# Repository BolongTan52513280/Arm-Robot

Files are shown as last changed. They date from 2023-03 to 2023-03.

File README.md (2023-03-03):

# Arm-Robot
A robot arm is developed. The robot arm consists of a base, two arms, two motors, two 
worm gears, two face-mount crossed-Roller bearings, two sensors, one pcb board and one 
Arduino board. 
此机械手臂机器人可抓取任何 15Kg 以下的物体并转移到指定地点。工作空间直径 1.4m, 稳定时间 1.3s, 超调为 5%，稳态误差 2.5%。
可用于物品运输，组件组装。我负责利用 Solidworks 设计机器人机械设计，并使用 Matlab 和 Simulink 设计控制系统，也负责机器人的测试，调试工作。

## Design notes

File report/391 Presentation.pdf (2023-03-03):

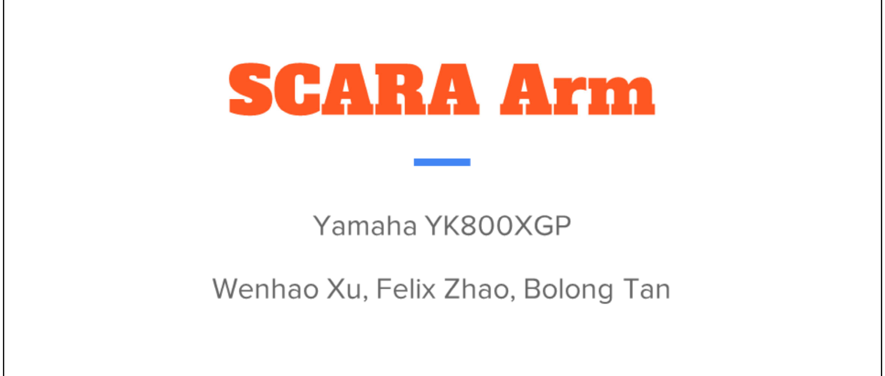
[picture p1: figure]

This slide deck will be for our final presentation for ELEC391 SCARA ARM. For team Yamaha YK800XGP.

For team organization, we split the work equally, Wenhao took care of the software section
Felix took care of the hardware section
And Bolong took care of the system section.
We also collaborate and help each other on their parts whenever possible.

For Electrical systems ECG, we need to design a circuit that will be able to support our motor selected.
We need to have a consistent nominal voltage and current that can satisfy our motors rated voltages.
We also need to not draw more current than we want from the wall plug to trigger the normally present wall plug fuses.
Our motor control board need to have a high switching frequency to reduce general component sizes and reduce our PCB size to be able to fit into our design’s base cavity. Lastly, of course we need basic circuit protection like overcurrent protections, voltage/current isolation, voltage/current surge protections and overheat protections.

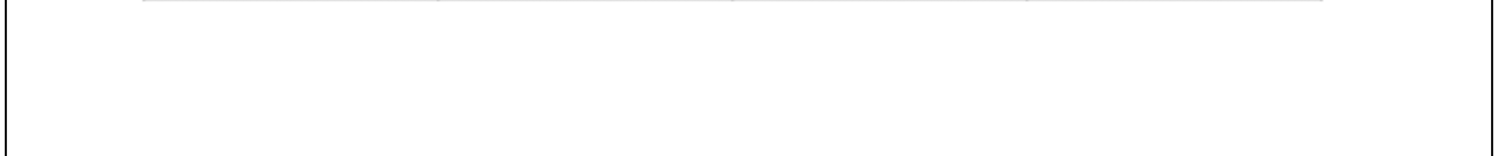
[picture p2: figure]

This is our mechanical system RCG.
The work space diameter we want to achieve is 1.2m and the height is 550mm.
One of our robot arm is 350mm and the other one is 250mm in length.
The full length of our robot arm is 600mm. The work space diameter is 2*600mm= 1.2m. The robot arm can reach any points within the work space.
For the payload, our goal is 15kg.
In our simulink and simulationx model,we used the 15kg load to simulate the whole model.
Even though the inertia due to the robot arm and 15Kg is pretty large.
Our design have successfully meet all these requirements.

This is our control system RCG. First we want an accurate arm, so we want to minimize steady state error and overshoot. We also want a fast arm, so we want to have good settle time and rise time.

As you can see this is our explode animation with the extra feature.

Our design consists of one base, three robot arms, three motors, three worm gears etc.

Two robot arms can move in the horizontal plane. Both arms can rotate 360 degree.

Our robot arm can also move in Z direction.

We used one extra motor and one extra worm gear.
1. Motor rotate shaft which is connected to worm gear (gear ratio is 30)
1. Worm gear is connected to the lead screw through the shaft
1. Worm gear and leads screws rotates at the same speed
1. A hex nut which connected to a rod is used
1. Hex nut cannot rotate because it is surrounded by a shell
1. Lead screw forces the hex nut to move up or down

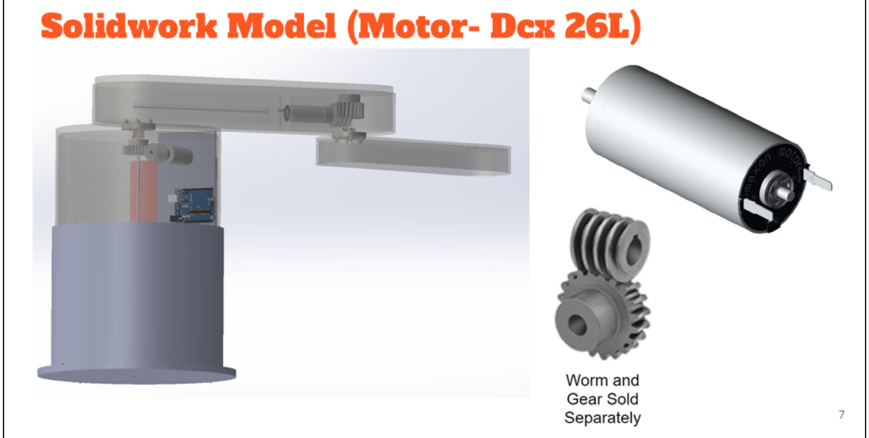
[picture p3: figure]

This is the solid work model we use without extra features whose arm can only move in horizontal plane.

Two robot arms can move in the horizontal plane. Both arms can rotate 360 degree.

The design consists of one base,two robot arms and two motors, two worm gears and etc.

The motor we chose is Dcx-26L.The reason we chose this motor is that:

1. Our robots arm length is 600mm which is quite long
1. We also want to pick a 15kg object

According to the calculation the torque we need is around 50Nm. The Dcx-26L motor is fits our requirement best.

Gear ratio of two worm gears we used are 20 and 30.

The advantage of worm gear is that:

1. Cheaper
1. Do not require too much space ( can be easily put into robot arm)

Two face-mount crossed-Roller bearing are used to make sure both robot arms can rotate freely in horizontal plane.

One face-Mount crossed-Roller bearing is used to connect base to arm.

The other one is used to connect two arms together.

For one of face-mount crossed-Roller bearing:

The inner part of face-mount crossed-Roller bearing is connected to the base using screws and nuts.

The inner part is fixed with respect to base.

The outer part of face-mount crossed-Roller bearing is connected to the robot arm using screws and nuts. It rotates at the same speed with arm.

For the other face-mount crossed-Roller bearing:

The inner part of face-mount crossed-Roller bearing is connected to the upper arm using screws and nuts.

The inner part is fixed with respect to upper arm..

The outer part of face-mount crossed-Roller bearing is connected to the lower robot arm using screws and nuts. It rotates at the same speed with lower arm.

For our power supply board design, with the previously mentioned RCG in mind, we developed out board to have:

- 5V, 12V and 24V output support for all the external ICs we need. (Arduino, Motor, Sensor)
- 40A maximum current supplied to the motor output.
- Stable voltage output under high current applications. (24±0.3V under 25A, 24±1V under 40A)
- Safety fuses in case of current surges for each output and transformers to prevent meltdowns.
- LED indicators and test points for easy debugging.
- Different thickness traces for high/low current areas, mounting holes for installation of the board, and a slot for arduino board.

The resulted board is able to support 2 26L motors and all other needed ICs with ease and satisfies our predefined design RCGs.

For our Motor Driver board or daughter boards, we designed our board to have:

- Only one PWM input needed to regulate the 24V input voltage utilizing the H-bridge circuit.
- Safety fuses in case of current surges for each input.
- Back emf protection using series of schottky diodes.
- Inrush current protection with the help of both the fuse and an inductor.
- An opto-coupler for current isolation for the arduino input side and ability to drive a 24V input with Arduino’s 5V output.
- Different thickness traces for high/low current areas, mounting holes for installation of the board

The resulted board is able to drive our motors with relative accuracy and satisfies our predefined design RCGs.

Next, for our optical sensor, we chose to use a on-market on-shaft optical encoder from US Digital : E4P miniature.
It is able to return 2 sets of square waves with varying phases depending on the shaft’s current angle from the home position.
With that in mind we can write a simple homing sequence like the one on the right:
1. Check both phases input, see if the two input values are the same/are we currently at base position (1% error accepted)
2. If they are not the same, determine which direction we need to move to be back to the home position.
3. Initiate the motor movement sequence until we reached the home position.
4. Raise the done flag so the system only performs homing sequence once upon startup.

Then we use simulink to model the control system and tune the PID controller. First we do 10 steps.
For the two motors:
- K = 0.4 Kp = 13.3 Ki = 1 Kd = 44.44 (joint 1)
- K = 0.4 kp = 8.7 Ki = 1 Kd = 18.9 (joint 2)
We would like to address the saturation introduced by the amplifier. After that, we do the heuristic tuning again and get
- K = 3 Kp = 50 Ki = 1 Kd = 10 (joint 1)
- K = 3 Kp = 40 Ki = 1 Kd = 10 (joint 2)
We have higher master to accommodate the saturation, and lowered the Kd to lower the overshoot to satisfy the RCG of minimizing overshoot, and raised Kp to make the motor have faster settle time (RCG).

We can see the step responses settle in less than 1.5 seconds, which is good for our RCGs.

We add more nonlinearities such as the nonlinearity introduced by sensor and static friction. For sensor, the encoder we choose has 1440 max pulses per revolution, which means the relative sensor can detect 1/16 degrees of angle. We convert the actual angle to degrees, times 16 and use matlab function floor to emulate the sensor’s behavior, then convert the whole number counts back to radians. For static friction we use a matlab function to make the actual angular velocity zero until the arms overcome the static friction. As the step response graph show, we still has a good settle time and low overshoot. Then we see if we can catch a moving target. As the result shows, we have a little overhead at start, but then we only have some lag after the target, which is good for our RCG of being fast.

We then use Simulation X to simulate the mechanical system. We set up a co-simulation system which connected Matlab Simulink and Simulation X. This helps us better study the effect of some factors such as gearboxes and gravity. The video shows step response of both the forearm and the arm. The picture is the result of Co-simulation of step of 2 and 1. We can see both can settle in about 1.5 seconds.

We can use inverse and forward kinematics to give the model x and y coordinate, and get the x and y coordinate of the current location. X axis is along the direction of arm on the model, and y is perpendicular to it. This shows the arm goes to (0.6,0), (0,0.5), (-0.5,0.2) and back, and repeat it a second time. Yellow line is x and blue line is y. We can see that it is fairly fast and relatively smooth, which meets our requirement.

Then we would like to envision how the arm would be used in real life situation. As the video shows, the arm would pick something up from a conveyor belt, and drop it on the other side.

For the extra feature, we achieve one extra degree of freedom.

Our robot arm can move in Z direction.

So, we can pick up things which are at different height.

In order to achieve this extra feature,we used one extra motor and one extra worm gear.

The gear ratio of the worm gear is 30.

1. Motor rotate shaft which is connected to worm gear
1. Worm gear rotates at the same speed with shaft
1. Worm gear is connected to the lead screw through the shaft
1. Worm gear and leads screws rotates at the same speed
1. A hex nut which connected to a rod is used
1. Hex nut cannot rotate because it is surrounded by a shell
1. Rotating Lead screw forces the hex nut to move up or down

The length of the rod which is connected to the hex nut is 75mm.

So the work space is a “cylinder area” with 1.2 meter diameter and 75mm height.

For the next extra feature, we designed a joystick controller for our arm.
It enables user to control the arm manually without the need to input coordinates into the system.
It uses interrupt to read the joystick’s analog input (0-1023) on both axis to help determine the direction our arm needs to move.
After we acquired the analog input, this input is scaled down and translated into an x-y coordinate change to our arm’s current position.
Then the new target coordinate is fed through our inverse kinematics function to return a target angle for our motors to process during the next interrupt routine.
The left picture shows our debug output for our design, it shows how the arm final coordinate changes in response to the user moving the joystick around.

This is a demo of the control of extra z-axis. We give it a sinusoidal wave and it moves up and down as the rack converts torque to force along z-axis, with good stability.

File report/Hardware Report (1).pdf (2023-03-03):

SCARA Robot – Hardware

White Paper | Updated – April 8, 2022

Chuyu Zhao, Group Yamaha YK800XGP, ECE, University of BC, Vancouver, BC, Canada

Abstract

In this project, we designed a fully customized power supply PCB that supplies power to all the ICs and motor driver boards, in addition to individual motor driver boards. The power supply mother board PCB consists of an Arduino Uno to act as a controller, a current booster circuit to boost the current output to support the motor, and voltage regulator ICs with smoothing capacitors to step down the voltages to desired values with minimum ripple. The Motor driver circuit consists of a power MOSFET H-bridge to drive the motor, and optocouplers to isolate the current and voltage from the PWM input side to protect the Arduino board.

In this paper, Section 1 describes the motor and optical encoder selection. Section 2 describes the resulted RCG from our component selections and design requirements. Section 3 describes the motherboard and driver circuit schematic designed and simulated in NI Multisim 14.2. Section 4 describes the Bills of Materials for the PCB.

Nomenclature

RCG | Requirements, Constraints, Goal
OTS | Off-the-Shelf
PCB | Printed Circuit Board
CAD | Computer-Aided Design
mNm | milli-Newton-Metres
CPR | Cycles Per Revolution
MOSFET | Metal-Oxide-Semiconductor Field-Effect Transistor
BOM | Bills of Materials
DOF | Degree of freedom
BJT | Bipolar junction transistor

### 1. OTS Part Selection

For easier calculations and design conformity, the same DCX 26L (Precious Metal Brushes) motor was chosen for the shoulder, elbow, and the plunger part (bonus DOF). The chosen motor can be found on pg. 93 of the Maxon Motor Catalogue [1] as shown in Appendix 1.

The DCX 26L (Precious Metal Brushes) motor we chose uses a 24V configuration. Such configuration was chosen as out of all configurations due to 24V one had the same maximum efficiency at 89% as all other configurations but provides the highest nominal torque of 52.3mNm with a stall torque at 384 mNm. In addition to that, the motor draws relative low current compares to other choices, allowing us to draw less current from the source and widening our PCB component selections.

For the micro controller, we choose to use an Arduino Uno board due to its high availability, high flexibility, good development tools/libraries and low cost (23$). The onboard chip ATMEGA328P supports up to 5 PWM outputs which is more than enough to support all three motors we will be running.

To allow us to sense the arm direction and movement speed to the microcontroller Arduino Uno, the US Digital E4P miniature encoder was chosen for all joints, selected from Prof. Leo Stocco’s personal webpage.
The 1000 CPR model was chosen for the highest resolution and cheapest price found for our selected motor shaft. For 31.77$, it has the same price as its lower resolution counterparts (100 CPR to 800 CPR), and it is also one of the cheaper 1000 CPR options available.

### 2. Design RCGs

With above components selected, using data from their own datasheet, we proposed the hardware part of the design’s RCG:

Specification | Requirement | Constraint | Goal
Nominal Voltage | 24V±2V | 24V±1V | 24V
Supply Voltages | 5V, 12V, 24V | | All
Max Current | 30A (both motor) | Max 50A | 40A
Switching frequency | 3kHz | | Maximum
Size | | 140mm*100mm | Minimum
Circuit protection | Overcurrent Optical isolation | | Maximum

Table 2.1: Hardware design RCGs The above RCGs are set to make sure that our system will be able to provide correct and stable voltage to all the parts connected, able to satisfy motor’s relative high current need, satisfy control system’s accuracy requirements and able to perform its task for an extended period of time while able to fit into our arm design.

### 3. Circuit Schematic Design

### 3.1. Mother board/Power Supply

For our power supply board design, with the previously mentioned RCG in mind, we developed out board to have:
(1): 5V, 12V and 24V output support for all the external ICs we need. (Arduino, Motor, Sensor) (2): 40A maximum current supplied to the motor output.
(3): Stable voltage output under high current applications. (24±0.3V under 25A, 24±1V under 40A)
(4): Safety fuses in case of current surges for each output and transformers to prevent meltdowns. (5): LED indicators and test points for easy debugging.
(6): Different thickness traces for high/low current areas, mounting holes for installation of the board, and a slot for Arduino board.

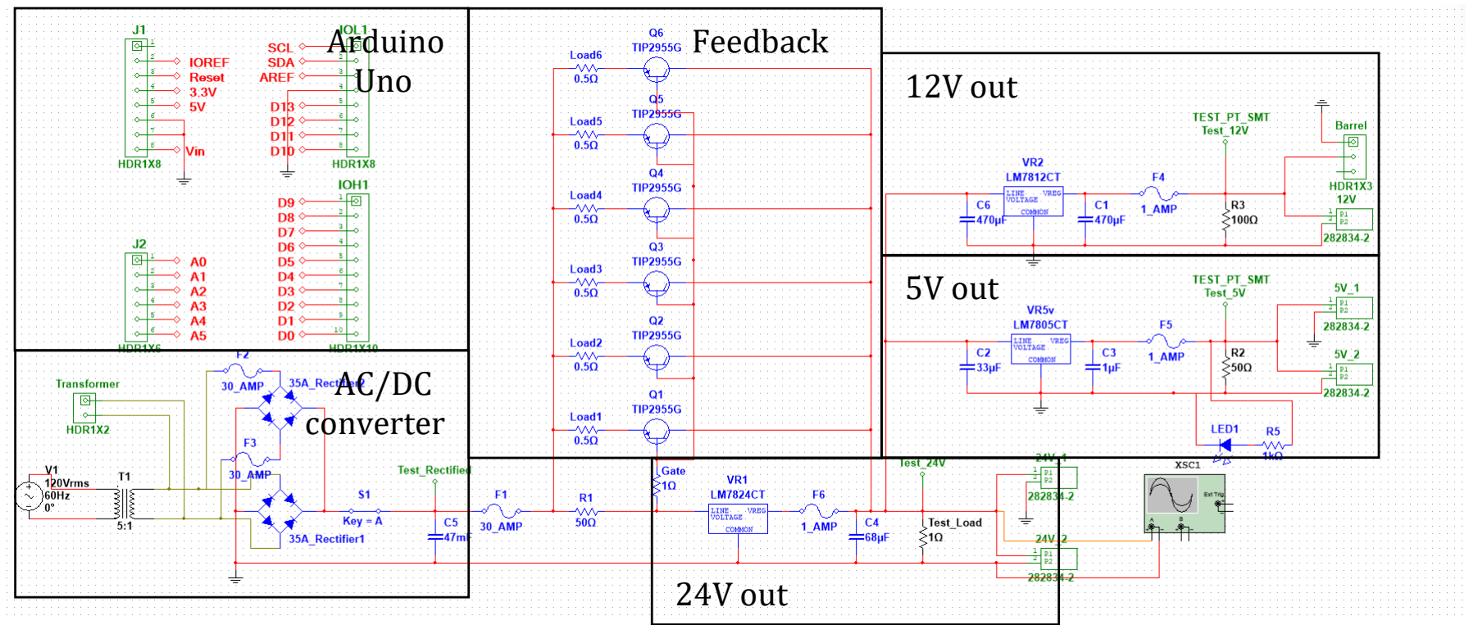
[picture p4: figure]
12V out; 5V out; 24V out; Feedback; AC/DC converter; Arduino Uno

Figure 3.1: MotherBoard Circuit Schematic for Interactive Simulation

To allow the power supply unit to meet our RCG, we used 3 different voltage regulators to achieve 3 different output voltages. The IC we chose (LM78xxCT) is cheap and can with withstand up to 40V (35V for 5V to 18V model) of input voltage, while maintain a very small output noise voltage of 45µV. With the help of bypass capacitors, we are able to achieve a very stabilized DC voltage output with a maximum peak to peak voltage of ~5.2mV under 25A of load current for the 24V side, 7.1µV at 12V side and 1.7µV at 5V side [2].. The output voltage under 25A motor load’s oscilloscope plot is shown below:

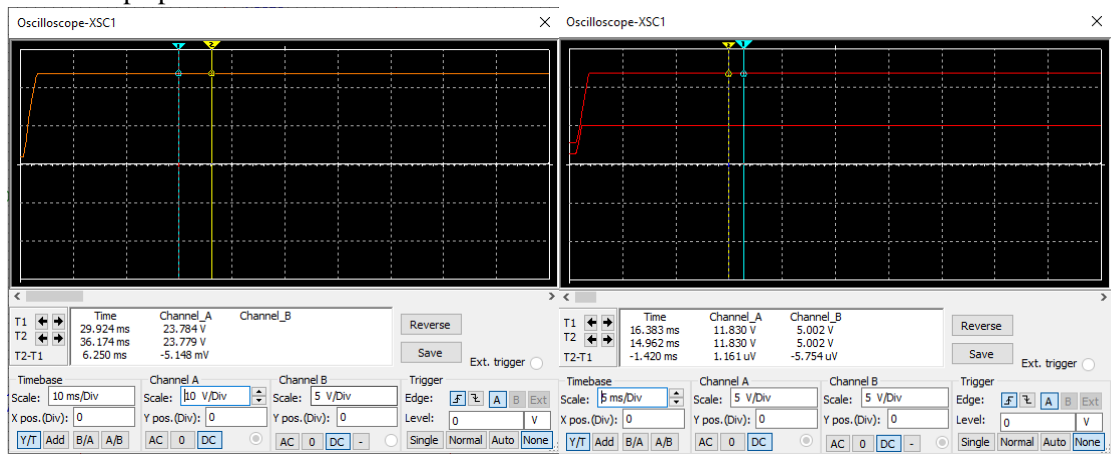
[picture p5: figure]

Figure 3.2: Oscilloscope readings for different output voltages For the current side, to achieve the targeted 40A output current capability, we designed a simple Power PNP BJT feedback network to “boost” the output current under 24V conditions on the collector side. The selected power transistor TIP2955G is able to withstand 60V and 15A of continuous current and voltage, making our transistor network able to handle up to 90A of current [2]., well taking care of potential current spike, in addition to its low cost and compact form factor, it is a solid option.
Going forward, the schematic is edited to correspond parts to packages, allowing us to forward the schematic to Ultiboard 14.2 to create the PCB.

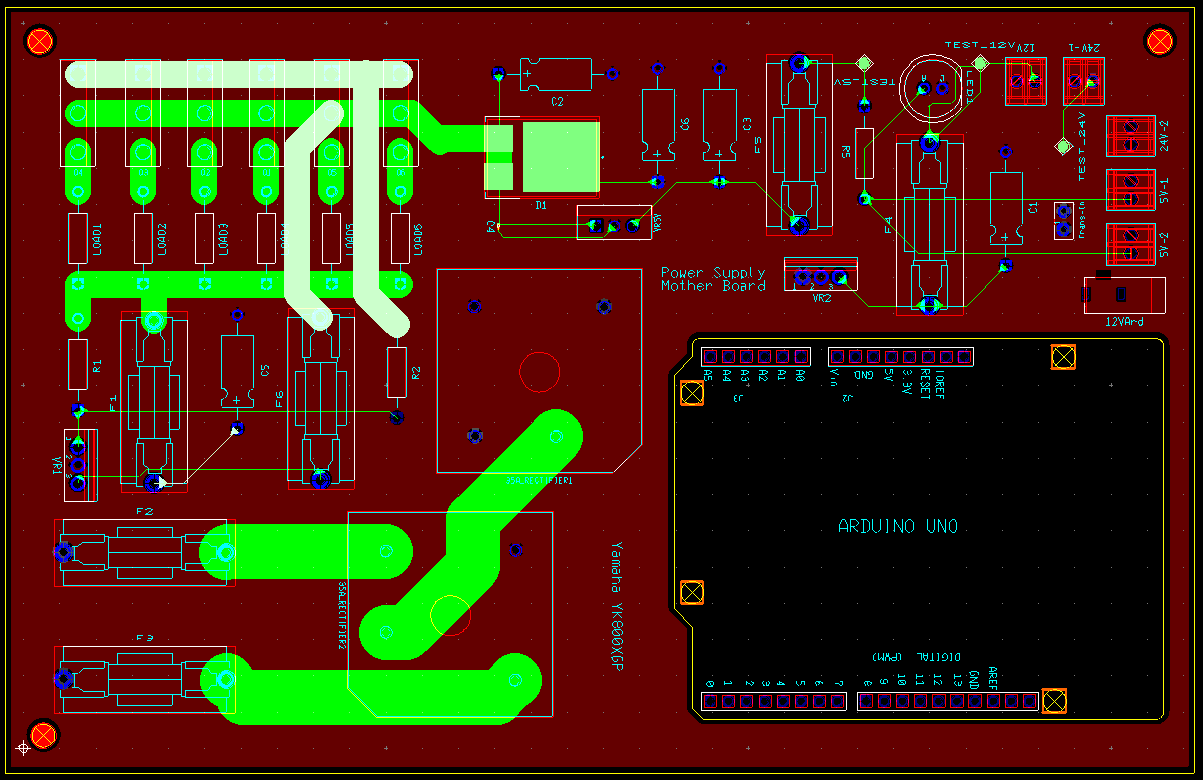
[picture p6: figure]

Figure 3.3: PCB Layout of the Mother Board in Ultiboard 14.2 As we can see from the figure above, we used 2 pin headers and barrel jacks to help connect our power supply circuit to motors and other ICs such as Optical sensors (5V) and Arduino Uno board (12V barrel jack). Utilizing power planes (Ground plane and a rectifier output plane) we are able to lower the connection planes to 2 layers. We have also considered about the maximum current that will flow between the pins and adjusted the trace width accordingly. The tool used to calculate trace thickness using current is shown in the Appendix below.
For the safety features, we added 1A fuses on each of the IC output side to make sure that the output current will not burn the chip, in addition to that, we have placed all the connectors on the edge of the board to reduce the risk of bending/damaging components when attempting to connect the ICs to the board. Below is our 3D rendering of the PCB design in Ultiboard 14.2:

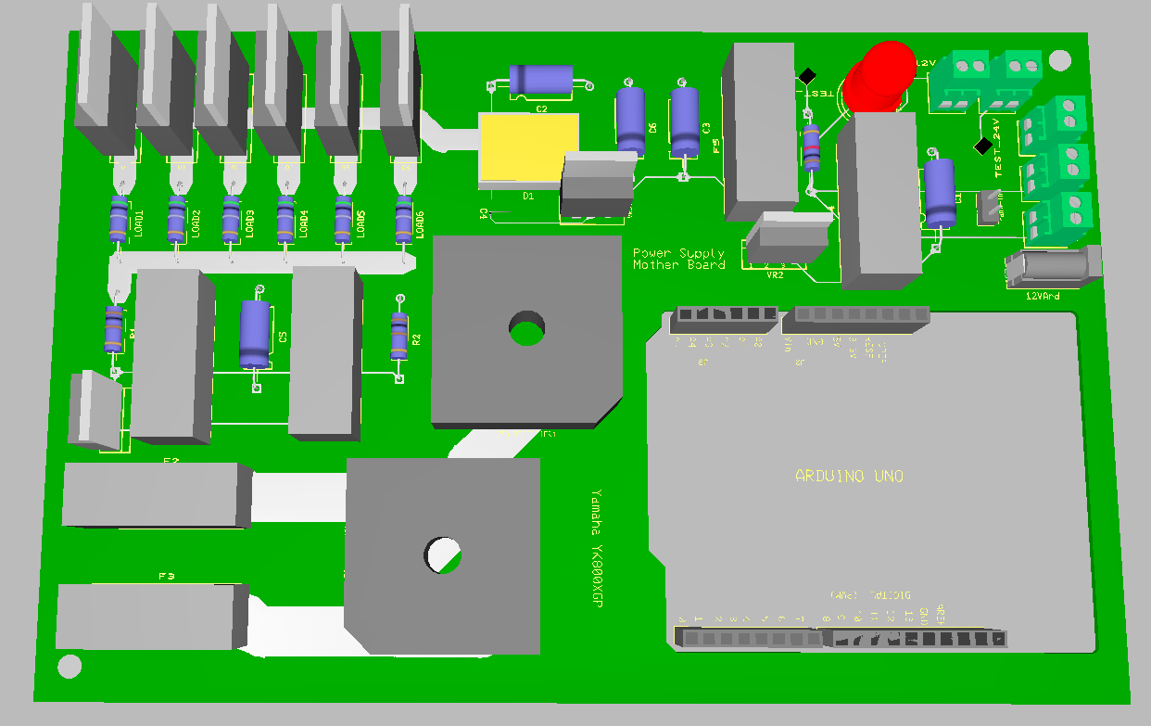
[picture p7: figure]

Figure 3.4: 3D Rendering of the Mother Board using Ultiboard 14.2

In addition to the safety features mentioned above, we have also added small features that allow easy testing for power users. As seen above in Figure 3.2-3.4, we added various test points at different voltage levels and an LED status indicator at the connector side to indicate the board’s current status.
For the last RCG, we have arranged all of our component in a compact, but not too crowded way, to achieve a 138mm x 87mm design size to perfectly fit into the body of out arm design.

### 3.2. Motor driver board/Daughter board

To allow for the bidirectional use of the motor, an H-Bridge-based circuit driven by an Arduino Uno 5V PWM input was created. As the motor model for all the joints is the same, the following schematicis repeated three times for each motor.

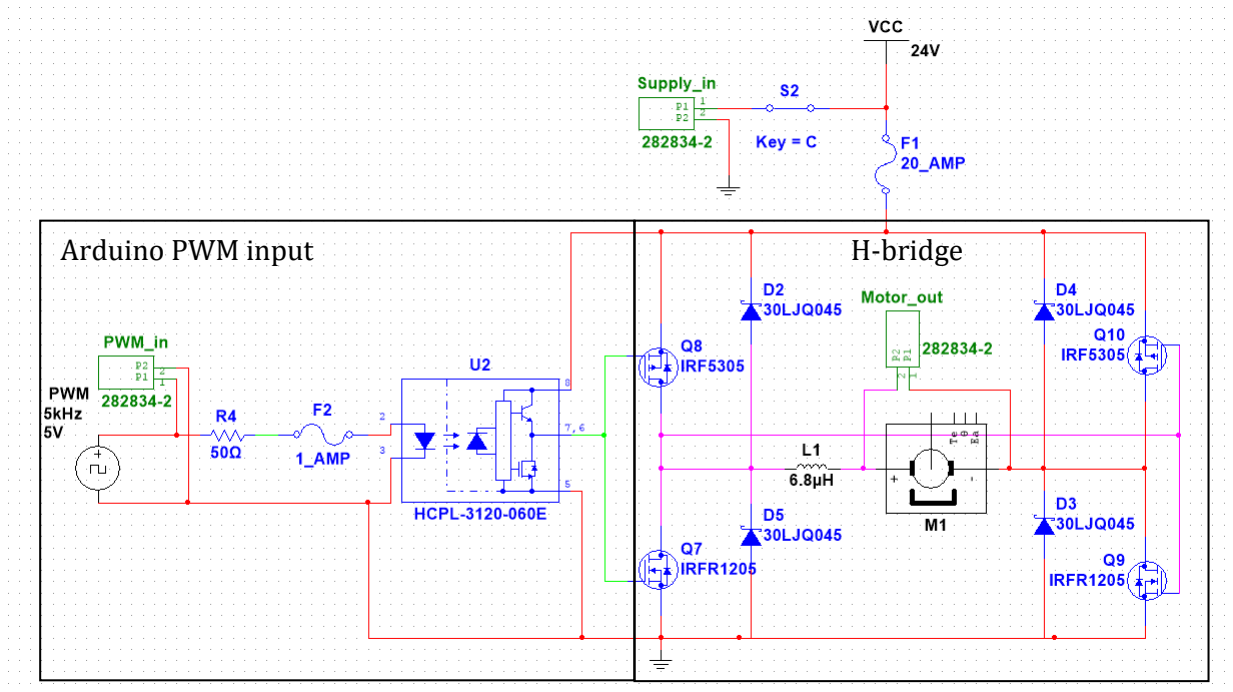
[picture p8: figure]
Arduino PWM input; H-bridge

Figure 3.5: Motor Driver Circuit in MultiSim 14.2

As seen, the H-Bridge is made of two pairs of N-Channel and P-Channel power MOSFETs with 4 schotty diodes for the back EMF. To simulate a relatively correct load, a DC PM brushed motor model from MultiSim 14.2 was used, in series with an inductor to smooth out the inrush current. The motor was modelled with the specs calculated from the actual DCX26L motor datasheet, making out simulation output as accurate as real-life measurement as possible.

For the power MOSFETs, the IRF5305 and IRFR1205 are capable of handling current up to 31A (44A for IRFR1205) and can both handle 55V of voltage with a very low internal resistance of 0.06Ohms and 0.027Ohms, which gives us very minimal voltage drop to make sure that our motor is able to receive a constant voltage supply of 24V±1V to keep the motor running. The schotty diode we chose to combat the back emf (30LJQ045) is also very compact and able to withstand 30A and 45V continuous voltage and current to support long term operation of the motors[2].

As for safety features, other than the fuses we placed on the 24V input side and PWM output side to protect the H-bridge and Arduino Uno, we also added an IGBT Gate Drive Optocoupler (HCPL-3120-060E) to make sure that we have enough voltage (24V) to drive the power MOSFETs while only utilizing one 5V PWM output from the Arduino Uno. At the same time isolating the high voltage side current form the low voltage side.

Exporting the Multisim layout to Ultiboard, we re-arranged components to form out daughter board PCB as shown below:

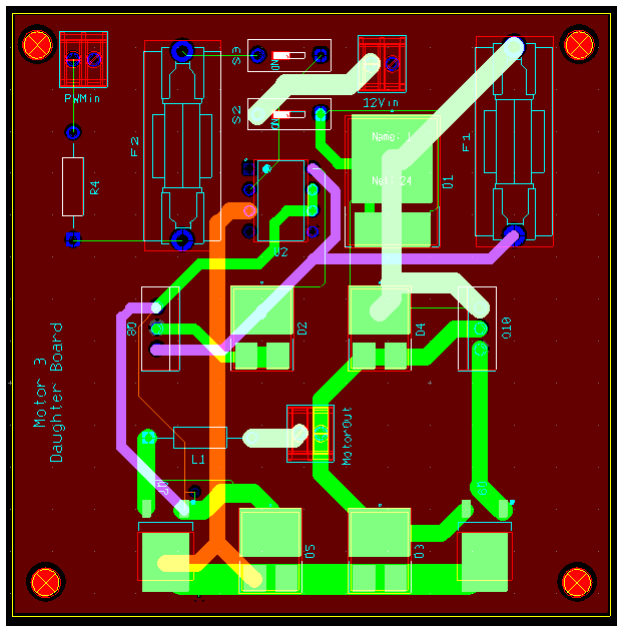
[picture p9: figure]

Figure 3.6: PCB Layout of Motor Driver Board in Ultiboard 14.2 As shown in Figure 3.4 above, we added 2 pin connectors for Arduino PWM input, power supply input and Motor supply output, with additional switches for testing user convenience. The detailed 3D rendering in shown below for the driver board:

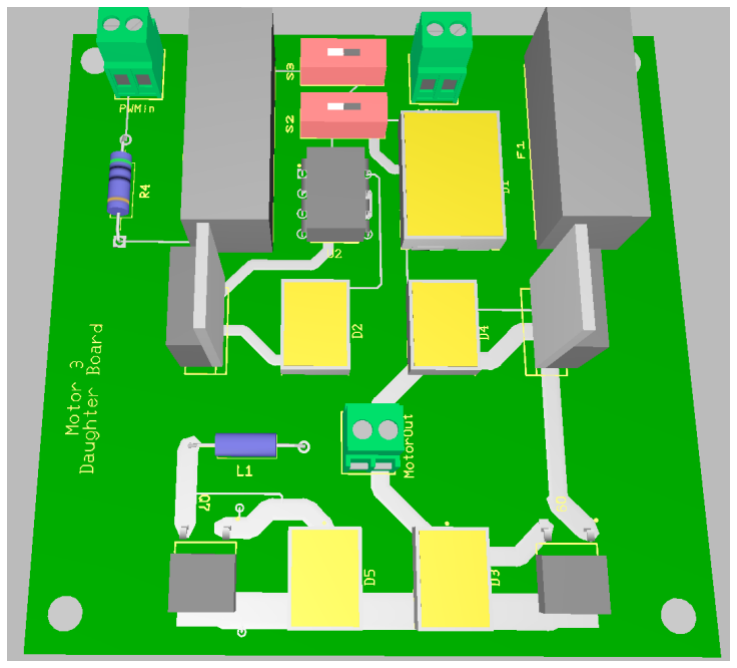
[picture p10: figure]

Figure 3.7: Driver Circuit PCB 3D Rendering With the help of power planes and careful component placements similar to the
Motherboard above, we are able to meet the RCG for board size with a very compact
65mm x 70mm board that can be fitted into our arm aside with the motor with ease.

To support the Simulink control system and to verify our own PCB design, the step response of the motor can be seen below:

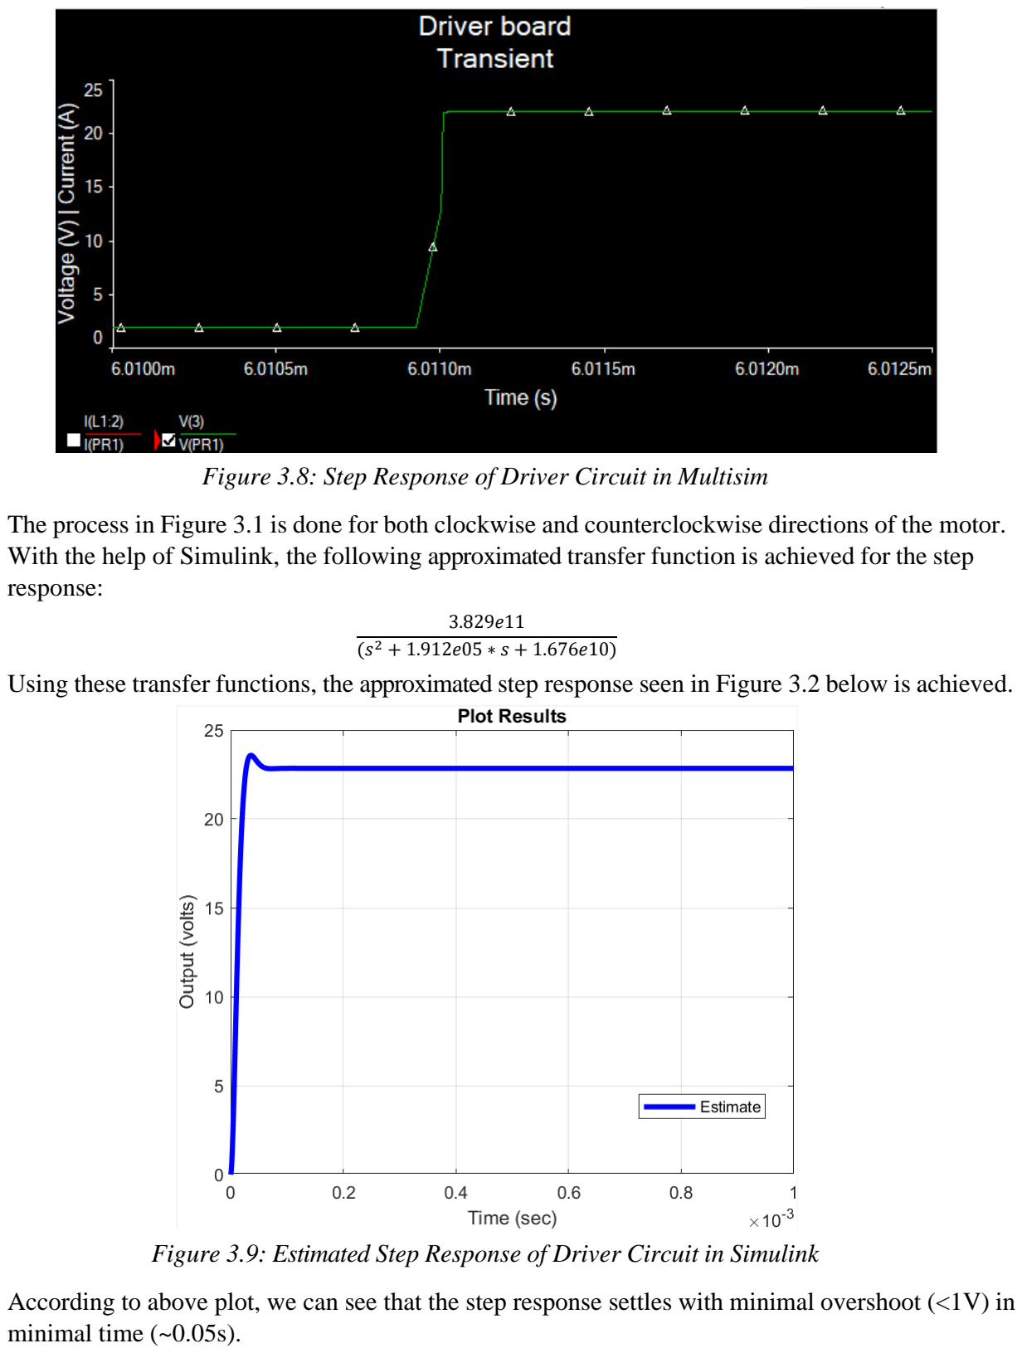
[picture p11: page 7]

Figure 3.8: Step Response of Driver Circuit in Multisim

The process in Figure 3.1 is done for both clockwise and counterclockwise directions of the motor. With the help of Simulink, the following approximated transfer function is achieved for the step response:

3.829e11
(s

2 + 1.912e05 ∗ s + 1.676e10)
Using these transfer functions, the approximated step response seen in Figure 3.2 below is achieved.

Figure 3.9: Estimated Step Response of Driver Circuit in Simulink

According to above plot, we can see that the step response settles with minimal overshoot (<1V) in minimal time (~0.05s).

### 4. Bills of Materials for the PCB

All prices are before tax in Canadian Dollars (CAD). Price data from Digikey.ca

The total cost of the BOM for 1 mother board and 3 daughter board (1 set) is $246.82.

Part | # of Components/Board pair | # of Component total | Total Price
Resistors | 9 | 11 | $3.63
Fuses | 9 | 13 | $32.17
Decoupling / Voltage Reg. Capacitors | 6 | 6 | $1.39
Optocoupler | 1 | 3 | $14.34
P-Channel Power MOSFET | 2 | 6 | $14.64
N-Channel Power MOSFET | 2 | 6 | $12.06
Voltage Regulators | 3 | 3 | $7.23
PNP BJT | 6 | 6 | $18.72
Connectors | 10 | 16 | $16.05
Schottky Diodes | 4 | 12 | $8.28
Arduino Uno | 1 | 1 | $23
E4P Optical Encoder | 1 | 3 | $95.31

References

[1] Prof. Leo Stocco. (2022). Maxon Motor Catalogue. Maxon Group. https://www.ece.ubc.ca/~leos/pdf/datasheets/Maxon/MaxonCat.pdf
[2] All Datasheets.com (2022). Electronics components data search. AllDataSheets. https://www.alldatasheet.com/
[3] Battle Electronics (2022). PCB Trace Width Calculator. Battle Electronics Inc. https://www.7pcb.com/trace-width-calculator.php

Appendix

### 1. Motor model used: DCX26L

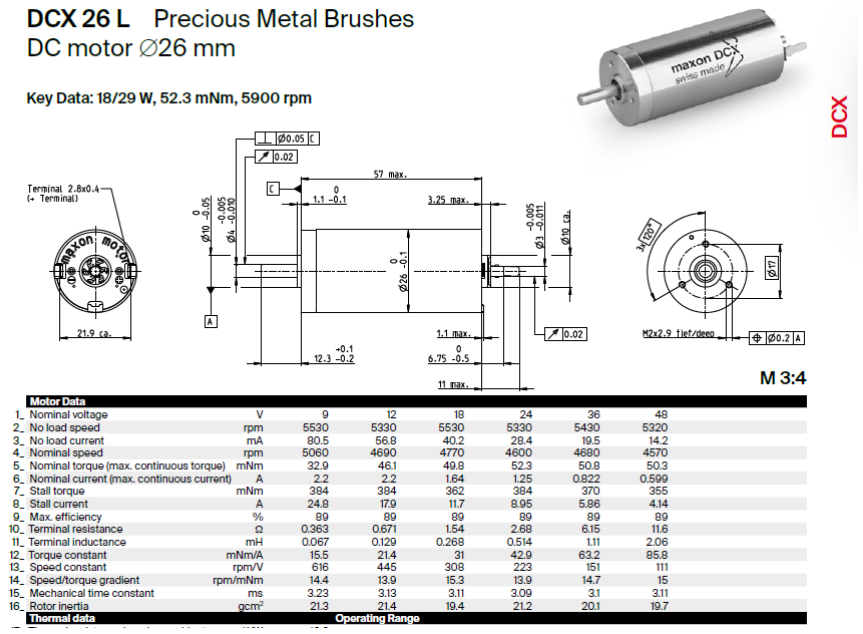
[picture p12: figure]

### 2. Trace thickness calculator [3]:

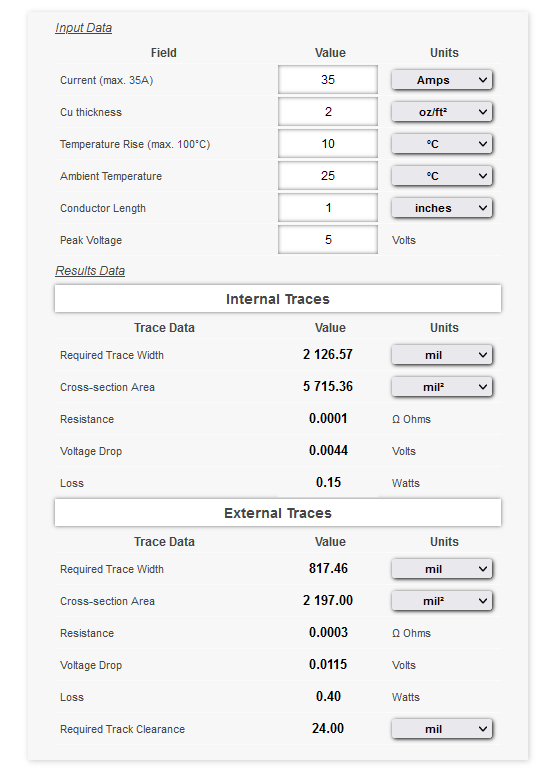
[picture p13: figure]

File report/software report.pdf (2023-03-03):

Software Report

Updated – April 8, 2022

Wenhao Xu

Abstract

This paper is about the software aspect of the project, including PID controller, actuators and C code.

Nomenclature

Joint 1 Shoulder joint of SCARA robot, & all associated components.

Joint 2 Elbow joint of SCARA robot, & all associated components.

### 1 Controller Design

### 1.1 RCG

There are two main concerns. First, it should be accurate to be useful. Next, it should be fast to be adapted by factories.

Requirement:

- Must be able to settle within 1.5 seconds

Constraint:

- Must not have overshoot larger than 20%

Goal:

- Minimize settle time
- Minimize rise time
- Minimize overshoot
- Minimize steady state error

### 1.2 System Models

The model of the control system is as following.

### 1.2.1 Amplifier Transfer Function

The amplifier circuit introduces some transient. It is modeled as a second order system for simplicity. The picture below shows a step response of the PCB driver circuit in multisim. The switch is flipped at 22ms, and a response is produced.

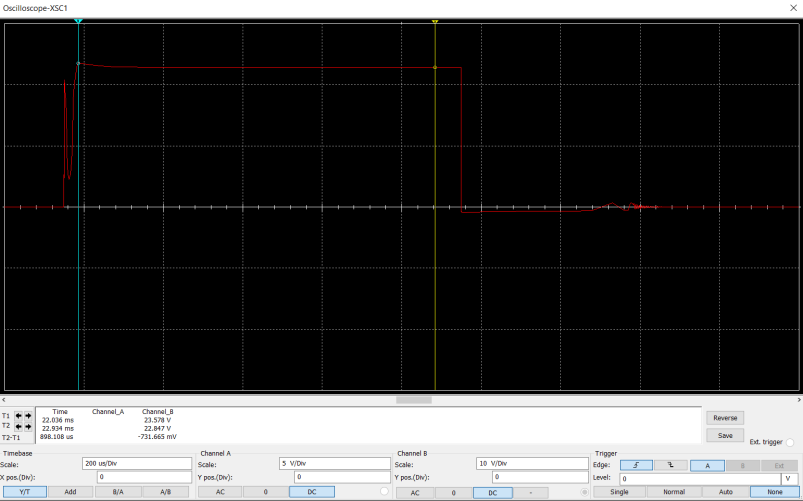
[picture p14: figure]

Fig 1. Step Response

From figure 1 it can be identified that the peak occurs at 0.036ms, with peak value 23.578 V. The system settles to about 22.847 V.

So, the overshoot value is 23.578-22.847 = 0.7310 V. The values can be used to estimate a second order system. The transfer function is found to be: (voltage/controller output)

3.829e11
s

2 + 1.912e5 s + 1.676e10

Plot the transfer function in Matlab, the graph is as the following.

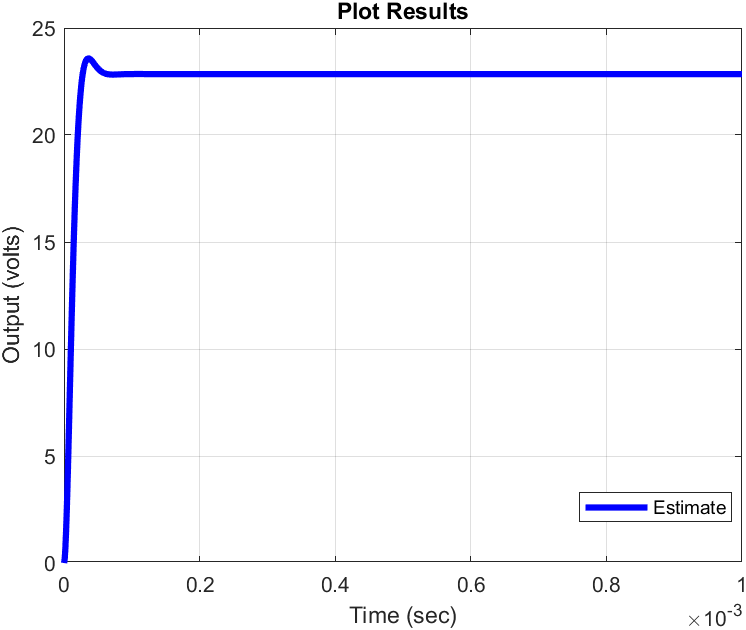
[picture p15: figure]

Fig 2. Step Response

The figure shows that there’s an overshoot which peaks at about 0.03 msecs, which is a good estimation of the driver circuit.

### 1.2.2 Motor

For the motor, first it has an electrical subsystem that can be modeled as a first order transfer function. To determine this system, the terminal resistance and terminal inductance are retrieved from the datasheet. [1]

Rw = 2.68 Ω

Lw = 0.514e-3 H

Then the transfer function is: 1
Lw ∗ s + Rw

=

1
0.514e − 3 s + 2.68

It is also worth noting that for a motor, there are:

τ = KmI

Ea = Kmω

From the data sheet above, the torque constant Km is 42.9 mNm/A = 42.9e-3 Nm/A.

### 1.2.3 Mechanism

For the two joints, two different gears are used.

### 1.2.3.1 Joint 1 (Shoulder)

The gear ratio used is i = 30. So, the mechanical impedance is 1
0.7833 s + 1.965e − 3

Combined, the mechanical system is as shown in the figure 3.

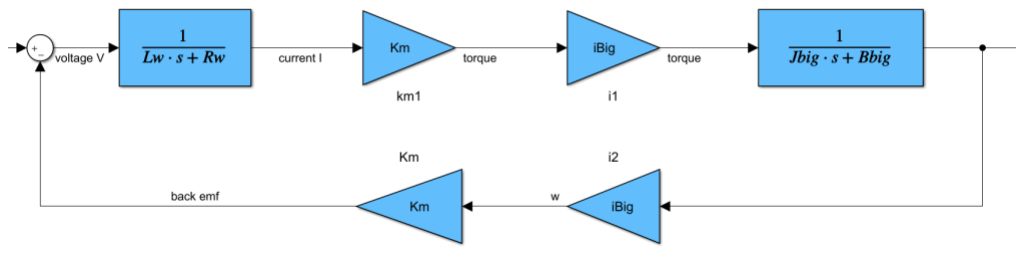
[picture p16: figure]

Fig 3. Mechanical System

### 1.2.3.2 Joint 2 (Elbow)

The gear ratio is i = 20. So, the mechanical impedance is

1
0.1131 s + 8.731e − 4

### 1.2.4 Sensor

Sensor introduces non-linearity. Based on different stage of modeling, there are different identifications.

### 1.2.4.1 Linear

At this stage, it is modeled as a linear system. So, it simply converts angle to counts, which is converted back to angles by the microcontroller. Thus, it is ignored for now.

### 1.2.4.2 Non-linear

For non-linear system, the sensor can be modeled as a Simulink subsystem like in the figure.

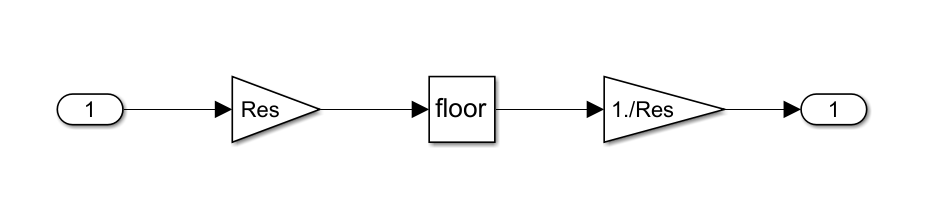
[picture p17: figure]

Fig 4. Sensor Model

The sensor is used as a relative sensor. The sensor has max pulses per revolution of 1440 from the data sheet [2]. Therefore, the sensor can see 360/4/1440 = 1/16 degrees of angle at best. The Res gain here first converts the radians to degrees, then multiplies it by 16 (so the least angle it can see is 1 count). That is

Res =

180
π

∙

1
1
16

Because the sensor outputs whole number counts, Matlab function floor is used. This introduces non-linearities. The 1./Res gain emulates the behavior of the microcontroller, where the angle in radians is recovered.

### 1.2.5 Control Frequency and Microcontroller

Control frequency is determined to be around 1300/s. The effect of sampling by the microcontroller is modeled as a transfer function:
2CF
s + 2CF

### 1.3 Sensor Filter

We chose the sensor because the sensor has a good resolution, which may not require future filtering.

To see if the sensor requires extra filtering, we investigated the sensor output versus input.

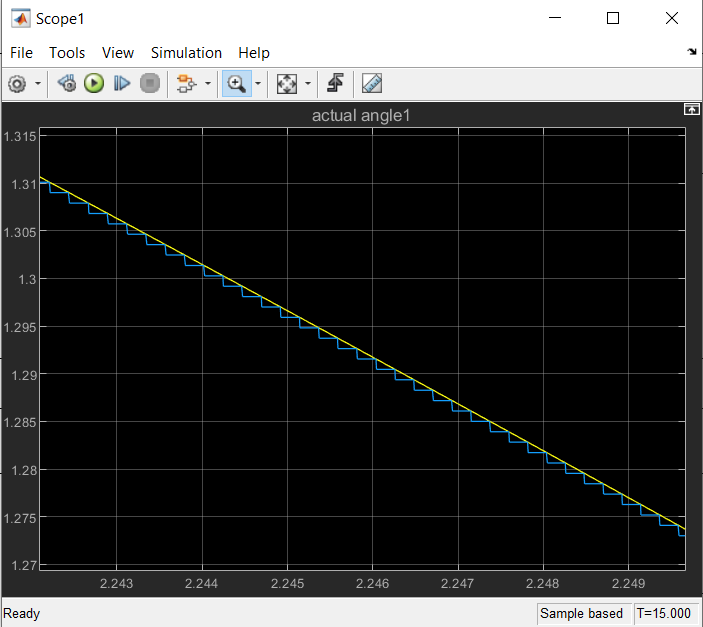
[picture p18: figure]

Fig 5. Sensor

In the figure, the blue graph is the output and the yellow one is input. As the figure shows, the sensor has a good resolution.

After evaluating the sensor, we decided that it does not require extra filtering.

### 1.4 Derivative Filter

The derivative filter is implemented in microcontroller. Thus, the unmodified derivative filter is the same as the microcontroller dynamics. After the tuning, the filter is not changed because the pole given by the filter is good enough.

1.5 10-Step Process

### 1.5.1 Joint 1

Step 1:

First, calculate the G = G1*G2*1/s and H=Hs*Hc. Hs is approximated as 1 in our system.

G1 is amplifier transfer function.

Ye = 1/(Lw s + Rw) is the electrical transfer function of motor.

Ym = 1/(Jbig s + Bbig) is the mechanical impedance of the joint.

G2 = Ye*Ym*Km*ibig/(1+Ye*Ym*Km*ibig*Km*ibig) – the overall forward branch.

Step 2:

Use the margin () function get Gain & Phase X-over frequencies (GXO & PXO). The margin graph is as below.

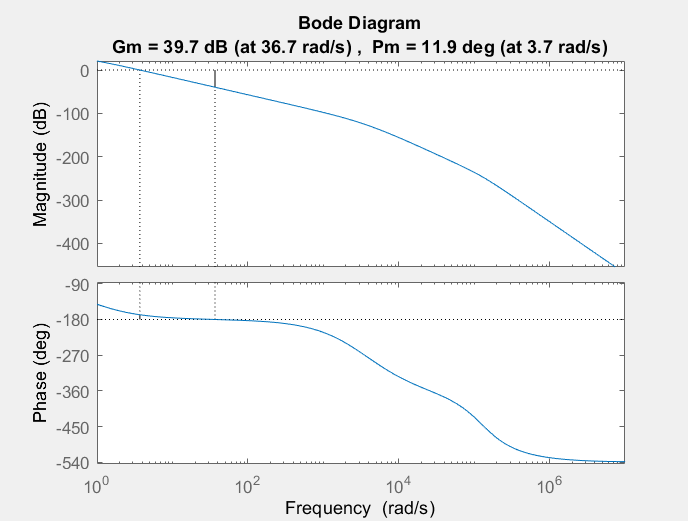
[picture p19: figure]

Fig 6. Margin

From the graph, there is

PXO = 36.7

so,

z = 3.67

Step 3:

P = 2*CF =2*1300 = 2600

Kp = 2/z-1/p = 0.5446

Ki =1

Kd = 1/(z*z) - Kp/p = 0.0741

D = Kp + Ki/s + Kd*p*s/(s+p)

Step 4:

Iterate. The final z value is chosen to be z = 0.15.

Step 5:

Zoom in the root locus of the open loop system G*H, around the origin there is

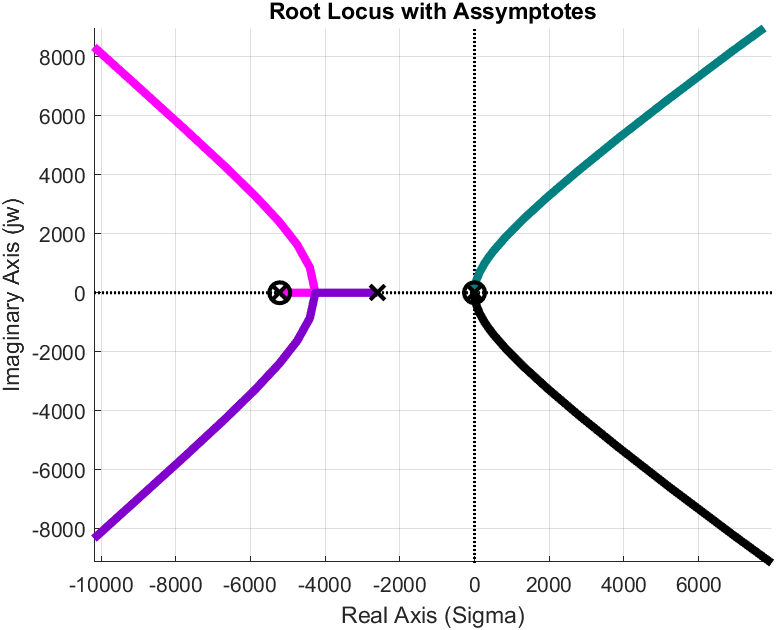
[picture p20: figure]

Fig 7. Root Locus

which is unstable. Then plot the root locus of open-loop system D*G*H.

Zoom in, it shows a better gain.

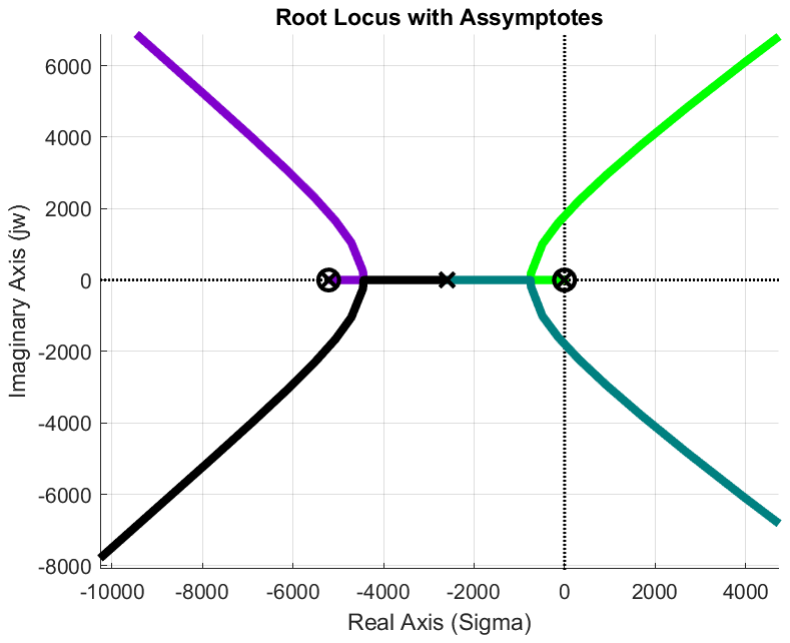
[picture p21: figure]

Fig 8. Root Locus Improved

To get the initial gain K, let K = 1/abs(freqresp(D*G*H,z)) = 6.4705e-4.

Step 6:

To check if the K improves the phase margin, plot the Nyquist contour of the open-loop system D*G*H and K*D*G*H.

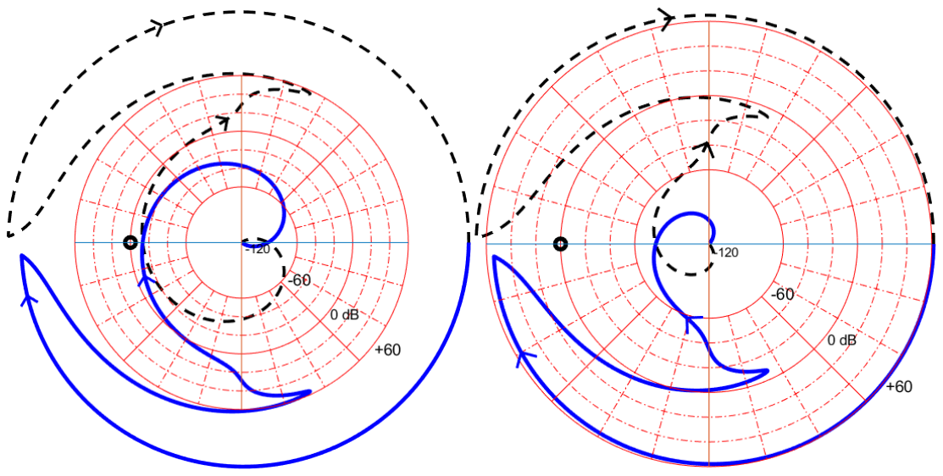
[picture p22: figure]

Fig 9. Phase Margin Improved

The left is the one of D*G*H and the right is the one of K*D*G*H. As the graphs show, the phase margin is improved because the -1 point now has more room to move.

Step 7:

Use step response of closed-loop transfer functions to choose a master gain K suitable to our RCG (fast and accurate). The figure below is produced in Matlab for comparison of different Ks.

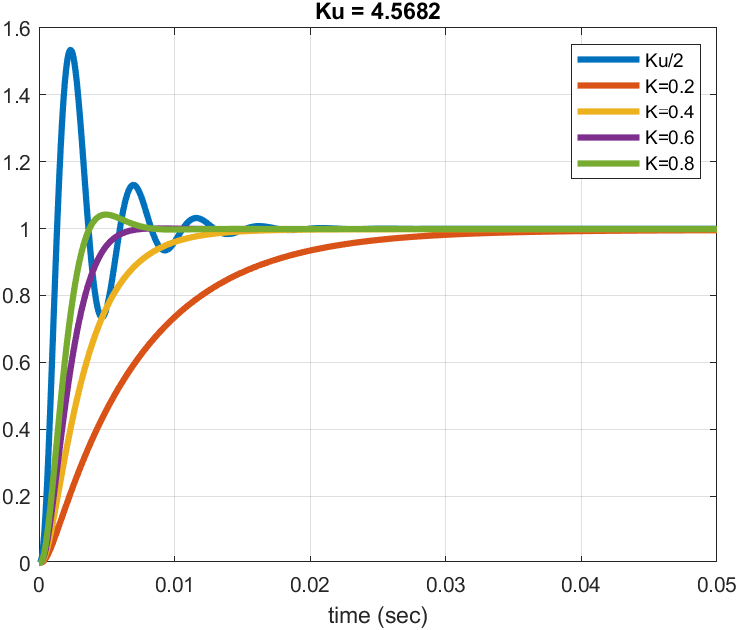
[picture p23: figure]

Fig 10. Step Response

All of the graphs settle in less than 0.05 seconds, which is favorable for our RCG. We also want to minimize the overshoot, so K should be at least less than 0.8. We chose K=0.4 for a good compromise between speed, accuracy and stability.

Step 8:

Use Simulink for heuristic tuning.

The systems have been identified in 1.2. Assemble them in Simulink as the figure below and run the model.

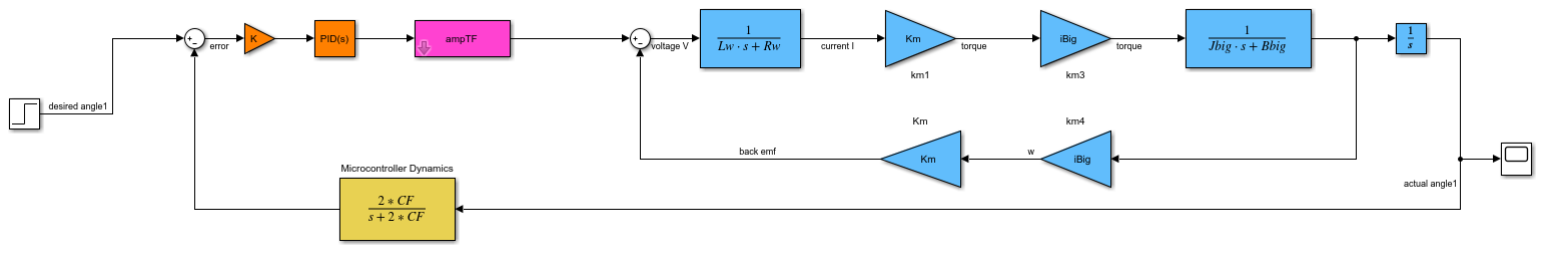
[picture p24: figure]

Fig 11. System

The wave we get from step 7 is already chosen to be the desired response. As the figure shows, it settles in 0.02 seconds with no overshoot.


Fig 12. Step Response

The K values are:

K = 0.4, Kp = 13.3, Ki = 1, Kd = 44.44

Step 9:

Now the non-linearities are brought back to the model.

The amplifier circuit has saturation effect on the voltage. It is modeled in Simulink as a saturation block.

The sensor can only output whole number counts, which is modeled as a gain that converts counts back to radians after the floor function after a gain that converts radians to counts.

The dynamic friction is linear time-invariant and is taken into account by the mechanical impedance, but static friction is dependent on past input. Thus, static friction is represented as a Matlab function (appendix).

After adding the non-linearities, the Simulink model is as following.


Fig 13. System

Use the system with non-linearities to get step response. The figure is the step response graph, which now has a very long settle time and large steady state error.


Fig 14. Step

The saturation slows down the rise time (and by extension settle time). The sensor introduces more steady state error.

Do heuristic tuning. The tuning should increase Kp (steady state error and rise time). First, because it is too slow, the master gain K was increased.


Fig 15. Tuning

Increase K from 0.4 to 3, the figure is the step response. Then Kp should be increased to lower the steady state error.


Fig 16. Tuning

When Kp is around 50 the graph is similar to the figure above.

Finally, we adjust Kd.

Fig 17. Tuned

After the first heuristic tuning, the step response is as shown in the figure. The response has good settle time and low overshoot, which satisfies our RCG.

The final test is the moving target. It sees if we have a good rise time, which is also what we want. Now, the input is a sinusoidal wave.


Fig 18. Moving Target

The figure shows the result of the test. After the startup, the output signal only lags the input signal a little. This shows that the system has a fast response, which meets our RCG.

The K values are

K = 3, Kp = 50, Ki = 1, Kd = 10.

### 1.5.2 Joint 2

The methods used for joint 2 are the same as joint 1.

Fig 19. Root Loci

Using z = 1.2, the open-loop root locus of D*G*H (right figure) is improved compared to G*H (left figure).


Fig 20. Step

Choose K=0.4 because it has a lower overshoot.

Do heuristic tuning.


Fig 21. Tuned

Compared to the original, tuned response is faster.

Now, K = 0.4, Kp = 8.7, Ki = 1, Kd = 18.9.


Fig 22. Tuned

This figure shows the tuned response in non-linear system. The settle time is good for our goal. The overshoot is small.

K = 3, Kp = 40 Ki = 1, Kd = 12.

### 1.6 Heuristic Tuning

The Simulation X system is as the figure.


Fig 23. Simulation X System

Using Simulink and Simulation X co-simulation, we can get more realistic mechanical system simulation. Give the angle at joint 1 (theta1) a step of 2 and the angle theta2 at joint 2 a step of 1. Observe the result (figure).


Fig 24. Tuning

The upper arm is heavier than we predicted. We have a large overshoot which forces us to do heuristic tune again. We would like to lower the value of Kp and Ki to reduce the overshoot. After tuning, the new K values for motor 1 is

K = 3, Kp = 40, Ki = 0.8, Kd = 15.

After tuning, the step response is as shown in the figure.


Fig 25. Tuned

The responses settle within 1.5 seconds. We evaluate our RCG and get our final K values.

Joint 1: K = 3, Kp = 40, Ki = 0.8, Kd = 15.

Joint 2: K = 3, Kp = 40 Ki = 1, Kd = 12.

### 2 Actuator

### 2.1 RCG

We established RCG for our actuator design based on the technical details of the product (Yamaha YK800XGP). (https://canvas.ubc.ca/groups/388809)

requirement:

- joint 1 must have angular acceleration >=0.25 rad/s^2
- joint 2 must have angular acceleration >=0.8 rad/s^2
- payload must be >=15kg

constraint:

- two motoes cost must not be higher than CA$500.

goal:

- maximize payload
- minimize cost

### 2.2 Motor 2.2.1 Joint 1

The design aims to pick up a 15 kg load. (two arms combined length is 600mm)

So, using the formula J=m*r^2

Load Inertia is: Jload = 15kg*0.6m^2 = 5.4 Nm

Using Solidworks mass property function we get arm inertia is:

Jarm = 0.42136

So the interia that joint 1 can feel is:

Jall = Jarm + Jload = 5.821 Nm

According to our design goal, we want our robot arm’s angular acceleration(a) to be 0.25 rad/s^2.

Using formula: torque = Jall* a = 1.4525 Nm

For joint1, we choose to use a worm gear and the gear ratio is 30.

Torque from motor = torque/30 = 0.0485Nm

In this way, we need a motor which can provide 0.0485Nm torque.

So, we choose the DCX26L EB KL 24V motor for joint 1.

DCX26L EB KL 24V motor can provide us 52.30 mNm torque which is higher than the requirement.

### 2.2.2 Joint 2

The design aims to pick up a 15 kg load. (fore arm length is 250 mm)

So, using the formula J=m*r^2

Load Inertia is: Jload = 15kg*250mm^2 = 0.9375 Nm

Using SolidWorks mass property function we get arm inertia is:

Jarm = 0.0497

So, the inertia that joint 1 can feel is:

Jall = Jarm + Jload =0.9872 Nm

According to our design goal, we want our robot arm’s angular acceleration(a) to be 0.8 rad/s^2.

Using formula: torque = Jall* a = 0.789776 Nm

For joint1, we choose to use a worm gear and the gear ratio is 20.

Torque from motor = torque/20 = 0.039488Nm

In this way, we need a motor which can provide 0.039488Nm torque.

So, we choose the DCX26L EB KL 24V motor for joint 2.

DCX26L EB KL 24V motor can provide us 52.30 mNm torque which is higher than the requirement.

### 2.3 Gear 2.3.1 Joint 1

The design aims to pick up a 15 kg load.

From the calculation, 1.4525 Nm torque is needed for shoulder joint1. However, the motor we choose (DCX26L EB KL 24V motor) can only provide us with 52.30 mNm torque.

We decided to use a worm gear whose gear ratio is 30.

Worm gears are used to transform the torque along x-axis to z-axis and increase the torque to drive the arms.

### 2.3.2 Joint 2

The design aims to pick up a 15 kg load. From the calculation, 0.9872 Nm torque is needed for shoulder joint2. However, the motor we choose (DCX26L EB KL 24V motor) can only provide us with 52.30 mNm torque.

We decided to use a worm gear whose gear ratio is 20.

Worm gears are used to transform the torque along x-axis to z-axis and increase the torque to drive the arms.

### 3 C code 3.1 PID

void PID(double speed_target, double current_speed, bool motor_id) {

The procedure PID accepts desired speed and actual speed to control.

double error = speed_target – current_speed; // error calculation

Calculate error, then calculate the PID branches respectively.

double ntegral = +(error + old_error) * deltaT / 2.0; // I
double ed = (error – old_error) / deltaT; | // edot
double x = Kp * error + Ki * ntegral + Kd * ed;

double pwn_duty = ((x / max_speed) * 255 > 255) ? 255 : (x / max_speed) * 255; // calculate duty cycle
double direction = speed_target > current_speed ? 1 : 0; | //
direction

We are using PWN to control the motor speed.

Finally, we instruct the driver circuit to product the PWM.

int motor_dir_pin1 = motor_id ? direction_control1_1 : direction_control2_1; // set the pins so this function is modularized
int motor_dir_pin2 = motor_id ? direction_control1_2 : direction_control2_2;
int motor_pwm_pin = motor_id ? PWM1 : PWM2;
digitalWrite(motor_dir_pin1, direction); // H bridge need to reverse for other half bridge
digitalWrite(motor_dir_pin2, !direction);
analogWrite(motor_pwm_pin, pwn_duty);

### 3.2 Homing Logic

First, we need a flag to indicate the homing is done, as homing only needs to be done once at start.

static bool homingdone;

After start, if our two sensors are not at the same phase (the relative sensor is not home), we need to do homing.

while (phase1 <= phase2 * 1.01 && phase1 >= phase2 * 0.99) // allowing 1% error {

Depending on the position, we adjust the arms either forward

while (phase1 < phase2) // if the motor is in the backward position {
forward();
}
stopMotor();
sleep(1000);

or backward.

while (phase1 > phase2) // if the motor is in the forward position {
reverse();
}
stopMotor();
sleep(1000);

Then we continue the loop.

}
homingdone = true; // homing done flag

### 3.3 Sensor Logic

Sensor outputs count instead of actual angle. So, we need to recover the angles.

First, we know from 1.2.4 the least detectable angle is 1/16 degrees.

#define RESOLUTION 16

The procedure sensor accepts the reading (count) and returns an angle in radians.

double sensor(int count) {

Next, we read the angle in degrees.

double deg = ((double)count) / RESOLUTION;

Finally, we return the radians.

return deg / 180 * 3.14;
}

### 3.4 Inverse Kinematics

The inverse kinematics is implemented and tested in Matlab.

function y = fcn(x1,y1)
arm1 = 0.35; %350mm upper arm length
arm2 = 0.25; %250mm forearm length

With known arm length, implement the inverse kinematics algorithm [3].

b2 = (x1^2 + y1^2 – arm1^2 – arm2^2)/(2*arm1*arm2);
s2 = sqrt(1-b2^2);
angle1 = atan2(arm2^2*s2*x1 + (arm1 + arm2*b2)*y1, (arm1 + arm2*b2)*x1 – arm2*s2*y1);
angle2 = -acos(b2);

Return the two angles.

y = [angle1,angle2];

### 3.5 Direct Kinematics

The direct kinematics is implemented and tested in Matlab.

The direct kinematics recovers the x and y coordinates given two angles. Since we know the direction of the angles, it is easy to know the coordinates.

function coord = fcn(angle1,angle2)
arm1 = 0.35; %350mm upper arm length
arm2 = 0.25; %250mm forearm length

x1 = arm1*cos(angle1) + arm2*cos(angle1+angle2);

y1 = arm1*sin(angle1) + arm2*sin(angle1+angle2);

coord = [x1,y1];

### 3.6 Testing

Next, we test the output of inverse/direct kinematics, the arm goes to (0.6,0), (0,0.5), (-0.5,0.2) and back.


Fig 26. Kinematics

The figure shows the x and y coordinates. We can see that the inverse and direct kinematics successfully control the path.

References

[1] Maxon catalog:
https://canvas.ubc.ca/courses/83907/files/18304886?module_item_id=3937630
[2] E4P Encode Data Sheet: https://people.ece.ubc.ca/leos/pdf/e391/Info/E4P_datasheet.pdf
[3] Inverse Kinematics in 2D: https://www.alanzucconi.com/2018/05/02/ik-2d-2/

Appendix

static friction

function y = fcn(w,tau)
Mg = 97.96;
mu = 0.002;
tau0 = Mg * mu;
stuck = (w == 0) & (abs(tau) < tau0); if stuck
y = tau;
else
y = 0;
end
end

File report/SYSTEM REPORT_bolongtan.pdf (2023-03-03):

Electrical and Computer Engineering | ELEC 391 | Apr 7, 2022

SYSTEM REPORT

GROUP Yamaha YK800XGP (https://canvas.ubc.ca/groups/388809)

Bolong Tan

Abstract

A robot arm is developed. The robot arm consists of a base, two arms, two motors, two worm gears, two face-mount crossed-Roller bearings, two sensors, one pcb board and one Arduino board.

In this paper, section one discuss the mechanical design of robot arm in detail. Robot arm is evaluated from structural, covers, interfaces, components, stress& strain, cable routing perspective. One explosion graph is provided at the end of section one.

Section two discuss the SimulationX model in detail. SimulationX model simulate how robot works and used to test the whole design. The test result of several test cases are discussed.

Section three discuss the application of the robot arm. It is evaluated from the special features, efficacy and cost perspective.

Nomenclature

$ | Canadian dollar
RCG | requirement, constraint, goal

MECHANICAL DESIGN
RCG

We established RCG(shown in table1) for our mechanical model based on the technical details of the product (Yamaha YK800XGP). (https://canvas.ubc.ca/groups/388809)

Table 1

Requirement:

1. Workspaceace diameter should be larger or equal to 1.1m
2. Design height should be higher than 700mm
3. The load that robot arm can carry should be heavier than 15kg
4. The torque that robot arm can produce 50 Nm
5. Cost should be less than 1000 dollars

Goal:

6. Workspaceace diameter should be maximized
7. Design height should be maximized
8. The load that robot arm can carry should be maximized
9. The torque that robot arm can produce should be maximized
10. Cost should be minimized
Specification | Requirement | Constraint | Goal
Work space diameter | >=1.1m | - | Max
Design Height | >=700mm | - | Max
Payload | >=15KG | - | Max
Torque | >=50Nm | - | Max
Cost | <=1000 dollars | - | Min

STRUCTURAL

### 1. Base support structure for shoulder joint


Figure 1 base shoulder

Figure1 shows the overall structure of the base shoulder joint.


Figure 2 base shoulder | Figure 3

As shown in figure2 and figure3, one face-mount crossed-Roller bearing is used to connect the base and up-Arm. As shown in figure 3, six screws and nuts are used to connect the outer side of the face-mount crossed-Roller bearing and up-Arm. Four screws connect the inner side of the face-mount crossed-Roller bearing and base. The inner side of the face-mount crossed-Roller bearing stays still to the base.

As shown in Figure 3.1, four small holes and one bigger hole are created at the top of the base. Four small holes are used to let four screws go through. The bigger hole is used to let the shaft go through.


Figure 3.1

### 2. Up-Arm support structure for shoulder joint


Figure 4

Figure4 shows the overall structure of the up-Arm shoulder joint.

Two face-mount crossed-Roller bearings are used. One face-mount crossed-Roller bearing is used to connect the base and up-Arm. Six screws and nuts connect the outer side of the face-mount crossed-Roller bearing and up-Arm. The outer side of the face-mount crossed-Roller bearing stays still to the Up-Arm. They both rotate at the same speed.


Figure 4.1

As shown in figure 4.1, the support structure is created to increase the structural strength. This support structure can let the shoulder joint withstand more load.


Figure 5

The other face-mount crossed-Roller bearing connects the Fore-Arm and up-Arm. As shown in figure 5, four screws connect the inner side of the face-mount crossed-Roller bearing and Up-Arm. The inner side of the face-mount crossed-Roller bearing stays still to the Up-Arm.

### 3. Fore-Arm support structure for shoulder joint


Figure 6

Figure 6 shows the overall structure of the Fore-Arm shoulder joint.


Figure 7

As shown in figure 7, six screws and six hex nuts are used to connect the outer side of the face-mount crossed-Roller bearing and Fore-Arm. The outer side of the face-mount crossed-Roller bearing stays still to the Up-Arm. They rotate at the same speed.


Figure 7.1

As shown in figure 7.1, the support structure is created to increase the structural strength. This support structure can let the shoulder joint withstand more load.

COVERS


Figure 8

Figure 8 shows the overall covers structure of the design.

As shown in figure8, the base cover is a cylindrical structure that is easy to be manufactured, and that would reduce the manufacturing cost. The upper arm cover and forearm cover have a similar structure. The upper arm cover and forearm cover are made as easy to manufacture as possible. Our team intends to lower the manufacturing cost. Cast Alloy steel is chosen to build the base, up-Arm cover and forearm cover. The reason why Cast Alloy steel is chosen is that Cast steel has the metallurgy manufacturing flexibility and strongest variability. This allows for complex shapes and hollow cross-section parts.

INTERFACES

Shaft connections


Figure 9 | Figure 10

As shown in figure 9 and figure 10, the shaft connected to the worm gear is part of the

Up-Arm. The shaft diameter is the same as the worm gear’s shaft diameter. The shaft

rotates at the same speed as up-Arm. The motor rotates the worm gear. The worm gear

then rotates the shaft and the shaft rotates the up-arm.


Figure 11

As shown in figure 11, a shaft connected to the worm gear is part of the fore-Arm. The

shaft diameter is the same as the worm gear’s shaft diameter. The shaft rotates at the

same speed as the fore-Arm. The motor rotates the worm gear. The worm gear then

rotates the shaft, and the shaft rotates the forearm.

Base mount


Figure 12

As shown in figure12, the base can be mounted to the ground and the table using four

screws.

PCB and Arduino mount


Figure 13

As shown in figure 13, the PCB board and Arduino are mounted to the base using three

screws and three hex nuts.

Base and up-arm mount


Figure 14

As shown in figure14, a face-mount crossed-Roller bearing is used to connect the base and up-Arm. Six screws and six hex nuts connect the outer side of the face-mount crossed-Roller bearing and up-Arm. The outer side of the face-mount crossed-Roller bearing stays still to the Up-Arm. They both rotate at the same speed. Four screws connect the inner side of the face-mount crossed-Roller bearing and base. As shown in Figure14.1, four small holes and one bigger hole are created at the top of the base. Four small holes are used to let four screws go through. The bigger hole is used to let the shaft go through. The inner side of the face-mount crossed-Roller bearing stays still to the base.

Figure 14.1

Forearm and up-arm mount


Figure 14.2 | Figure 14.3

A face-mount crossed-Roller bearing is used to connect the Fore-Arm and up-Arm. As shown in Figures 14.2 and 14.3, four screws are used to connect the inner side of the face-mount crossed-Roller bearing and Up-Arm. The inner side of the face-mount crossed-Roller bearing stays still to the Up-Arm. Six screws and six hex nuts connect the outer side of the face-mount crossed-Roller bearing and Fore-Arm. The outer side of the face-mount crossed-Roller bearing stays still to the Up-Arm. They rotate at the same speed.

COMPONENTS

We integrated all the necessary electronics and mechanical parts in our CAD model, including:
Screw: 91290A123_Black-Oxide Alloy Steel Socket Head Screw
Nuts: 90592A085_Steel Hex Nut
Motor: DCX26L EB KL 24V
motor selection:

The design aims to pick up a 15 kg load.(two arms combined length is 600mm)

So using the formula J=m*r^2

Load Inertia is: Jload = 15kg*0.6m^2 = 5.4 Nm

Using Solidworks mass property function we get arm inertia is:

Jarm = 0.42136

So the interia that joint 1 can feel is:

Jall = Jarm + Jload = 5.821 Nm

According to our design goal, we want our robot arm’s angular acceleration(a) to be 0.25 rad/s^2.

Using formula: torque = Jall* a = 1.4525 Nm

For joint1, we choose to use a worm gear and the gear ratio is 30.

Torque from motor = torque/30 = 0.0485Nm

In this way, we need a motor which can provide 0.0485Nm torque.

So, we choose the DCX26L EB KL 24V motor for joint 1.

DCX26L EB KL 24V motor can provide us 52.30 mNm torque which is higher than the requirement.

Worm gear: 57545K639_Steel Worm & 57545K779_Metal Worm Gear. The gear ratio is 30.
We chose this model of gear primarily based on the consideration of the Torque requirements and Price.
The steel worm is connected to the motor through a shaft.
The Metal Worm Gear is connected to the up-Arm through a shaft.

Worm gear: 57545K644_Steel Worm & 57545K819_Metal Worm
Gear.
The gear ratio is 20.
We chose this gear model primarily based on the consideration of the Torque requirements and Price.
The steel worm is connected to the motor through a shaft.
The Metal Worm Gear is connected to the fore-Arm through a shaft.

Arduino and customized PCB circuit: Arduino UNO
PCBs and Arduino are mounted on the upper shelf of the Base.

Face-mount crossed-Roller bearing:2010N11_Face-Mount Crossed-Roller Bearing We chose this gear model primarily based on the consideration of the magnitude of pressure that the base would feel and the Price.

STRESS AND STRAIN

Solidworks built-in SimulationXpress function is used to exam the amount of force each part is able to bear. The test result shows that all part could able to withstand around 234KG of the load. However, the face mount bearing used to connect the two arms would experience a maximum of 200KG of load. So, the Face-mount crossed-Roller bearing could be weakest part in our design.

BASE GEOMETRY

Figure 4 | Figure 4.0

As shown in figure4, the extra base support structure aims to increase the structural strength of the base. The extra base support structure connects the base cover and base. This support structure can let the base withstand more load. The extra base support structure shown in figure 4.0 aims to increase the structural strength of the base cover. It is helpful to stabilize the screws which connect the base cover and face mount bearing together.

ARMS GEOMETRY

Up Arm


Figure 4.1

As shown in figure4.1, the support structure for the joint is created to increase the structural strength of the shoulder joint. This support structure can let the shoulder joint withstand more load. The “X-shape” up-arm support structure shown in figure 4.1 aims to increase the structural strength of the up arm.

Fore Arm

Figure 4.2

As shown in figure4.2, the support structure for the joint is created to increase the structural strength of the shoulder joint. This support structure can let the shoulder joint withstand more load. The “X-shape” fore-arm support structure shown in figure 4.2 aims to increase the structural strength of the up arm.

CABLE ROUTING


Figure 15 | Figure 16

As shown in figure 15, the tube is hollow and there are two holes in the tube. The cable

can go through the hole and the hollow tube in figure15 to reach the hole shown in

figure16 which is located on the up arm. The hollow tube is located at the center of the

base. In this way, when the up arm rotates, the cable would not to be stretched to cause

some damage.


Figure 17

After the cable goes through the hole shown in figure 6, the cable will go through the

hollow tube shown in figure 17.

ASSEMBLY

EXPLOSION VIEW OVERVIEW


Figure 9 Explosion graph

Figure 9 shows the Explosion graph. All the components used in the design are labeled with a name and numerical number.

Components in Figure9:

Six screws and hex nuts-1:

Screw: 91290A123_Black-Oxide Alloy Steel Socket Head Screw

Nuts: 90592A085_Steel Hex Nut

Motor and worm gear-2:

Motor: DCX26L EB KL 24V

We choose this model of the DC motor primarily based on the consideration of the Torque requirements and Price.

Worm gear: 57545K639_Steel Worm & 57545K779_Metal Worm Gear

The gear ratio is 30.

Three screws and hex nuts-3:

Screw: 91290A123_Black-Oxide Alloy Steel Socket Head Screw

Nuts : 90592A085_Steel Hex Nut

Screws-4:

Screw: 91290A123_Black-Oxide Alloy Steel Socket Head Screw

Base -5:

Base is mounted to the ground using 4 screws (91290A123_Black-Oxide Alloy Steel Socket Head Screw).

Forearm cover -6:

Forearm cover was created using Solidwork.

Motor &Worm gear-7:

Motor: DCX26L EB KL 24V

We choose this model of the DC motor primarily based on the consideration of the Torque requirements and Price.

Worm gear: 57545K644_Steel Worm & 57545K819_Metal Worm Gear

The gear ratio is 20.

Face-mount crossed-Roller bearing-8:

face-mount crossed-Roller bearing:2010N11_Face-Mount Crossed-Roller Bearing

Six screws and hex nuts-9:

Screw: 91290A123_Black-Oxide Alloy Steel Socket Head Screw

Nuts : 90592A085_Steel Hex Nut

Four screws-10:

Screws: 91290A123_Black-Oxide Alloy Steel Socket Head Screw

Up arm cover-11:

Up arm cover: Up arm cover was created using Solidwork.

Base cover-12:

Base cover: The base cover was created using Solidwork.

SIMULATIONX DESIGN

RCG

For the SCARA arms, we have two main concerns. First, it should be accurate so that it can be used in an assembly line. Next, it should be fast to be competitive in the market. Requirement:
- Must be able to settle within 1.5 seconds
Constraint:
- Must not have an overshoot larger than 20% Goal:
- Minimize settle time
- Minimize overshoot
- Minimize steady-state error

Diagram
The diagram view of the simulation x model is shown in the figure10 below. The torques go through the gearboxes and rotate the joints.


Figure 10

Here, the friction before the gear is the friction of the motor. The friction is 2.1828e-6 Nms/rad (from the motor datasheet).

Worm gears transform the torque along the x-axis to the z-axis and increase the torque to drive the arms.

We used the worm gear model available in Simulation X to simulate the worm and gear system of our design. The figure shows the parameters of worm gear 1 for the shoulder joint1 (30:1). The Pitch angle is inferred to be around 27 degrees because it should be near the normal

pressure angle.

The arm (up-arm), forearm and base are imported as STL files. The inertia and mass are evaluated using SolidWorks. The robot arms are evaluated with motors, gears and bearings installed, so the respective inertia is accounted for.

The joints allow the arms to rotate. We decided to model the joints as ideal no-loss joints because bearings are used to reduce the dynamic friction, and the static friction is given in the Simulink model. More about the bearings are discussed below. Joint 1 drives the up-arm around the base, and joint 2 makes the forearm rotate around the up-arm.

At the end of the forearm, a 1kg load is attached to simulate the working condition of the arm.

The sensors observe the angle and angular velocity of the arms and send them back to the Simulink Co-simulation coupling through the multiplexer. The coupling also gets the torque output of the Simulink model and sends them to the torque block as the torque the system is experiencing.


Figure 10.1

As shown in the figure10.1, Simulink receives the output from SimulationX and use these signal to update the model.

ADJUSTABILITY

Some of the parameters are extracted and put into constant returning functions. For example, as shown in the figure10.2 below, the frictions of two joints and the mass of the two arms are factored out and out into functions.


Figure 10.2

This approach allows us to quickly test out the design and adjust the parameters of each component in the system.

RESULTS

Give the up arm a step function input of 2 rad, and the forearm a step function input of 1 rad, the resulted angle of co-simulation is shown as figure 10.3 :


Figure 10.3

The figure shows that the arms settle within 1.5 seconds, which satisfies our goal of settling within 1.5 seconds.

Next, we test the output of inverse/direct kinematics, the arm goes to (0.6,0), (0,0.5), (-0.5,0.2) and back.

Figure 10.4

As shown in figure 10.4. The yellow represent the X location of arm, and blue line represent the Y location of arm. The arm moves relatively fast and smooth, but as shown in the middle of the graph, the accuracy is lowered as the arms are in constant movement. We evaluate our RCG and decided that given enough time, the arm will reach the point, so it is more important to have faster arms.

Saturation and non-linearity avoided

In Simulink model, a saturation block is used to prevent the voltage from being too high which could break the motor. The saturation block adds Non-Linearities to the control system. In order to avoid non-linearity, the step 9 and 10 in 10 step calculations are used.

SENSITIVITY

To account for bearing wear, the rotational losses block is added to the two joints. The efficiency is chosen to be 80%. The wore bearing would have an increased friction due to wearing out, so the torque transported would be less. Thus, the rotational loss is added to the diagram.

APPLICATION

RCG

We established RCG for our mechanical model based on the technical details of the product (Yamaha YK800XGP) (https://canvas.ubc.ca/groups/388809) as follow:

Requirement:
- Must be able to grab >=15kg object
- The settling time must be <= 1.5s
- cost must be <= 1000 dollars
Constraint:
- Must not have an overshoot larger than 20% Goal:
- Minimize settling time
- Minimize overall cost
- Maximize the weight of the load it can carry

SPECIAL FEATURES

Our robot arm is designed to work in a flow shop. It is mounted on the table and used to move some objects from one place to another place. That requires our robot arm have a large workspace diameter. In this way, we designed our robot arm length to be 600mm, and workspace diameter is 1.2m.

One workshop could need multiple robot arms. To lower the cost, the base cover, the upper arm cover and the forearm cover are made easy to manufacture, so different components can be manufactured using the similar mold.

EFFICACY

Our robot arm design satisfies all the RCGs based on the Simulationx test result and cost calculation below. We test our SimulaitonX model, carrying a 15kg object. The test result shows that our robot arms can reach the desired location within 1.5s. From the calculation, the overall cost is 980 dollars, which satisfies the requirement.

COST

According to our RCG, we want to minimize the cost.

When we choose the component used to build the robot arm, our team always chooses the cheapest option except for the motor. Two motors cost 462 dollars in all. In the robot arm, 27 screws and 15 hex nuts are used, which cost 191 dollars in total. Two face-mount crossed-Roller bearings cost 36 dollars. Two worm gears cost 80 dollars. Two sensors cost 80 dollars. One Arduino and one PCB cost 60 dollars. For the base cover and arm cover material, Alloy steel is chosen. The total cost of the design is around 980 dollars.

Trades off

We keep our robot arm shape as simple as possible to minimize the manufacturing cost. When we choose the component used to build the robot arm, our team always chooses the cheapest option except for the motor. If we can ignore the price of components used in our design, we can further improve the performance of our design. For example, we can choose better ball bearings and screws to make the arm carry a heavier load.

### Appendix

J = m*r^2

Torque = J*a

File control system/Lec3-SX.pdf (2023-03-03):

# Simulink


Example System
- 2 identical systems
- Step response
- P-Controller (orange)
- Amplifier (pink)
- Electrical motor model (blue)

Elec 391 - Supplementary Notes

# Actual & Approx Inertia


Example System
- Yamaha pendulum
- Actual part from SolidWorks
- STL format
- Sphere mass
- Located at COM
- Arm transparent -> no dynamics
- Identical motor (rotor) dynamics

# Co-Simulation

Simulink ITIFct2 | SimulationX TCP/IP


run error if wrong

Display Results
• Drag & drop
• Minor differences in inertia

Material; Right-Click

From SolidWorks
- Apply material to part
- Shows up in design tree

Inertia; Evaluate / Mass Properties; Cen of Mass; O/P Coord Sys; Z-Axis Into Page Rotation Axis

Evaluate Tab
- Model Properties
- Material density
- Mass
- COM
- Inertia Tensors
- Choose co-ordinate centre wisely to get useful info

Results; Properties

Display Results
- Drag & drop
- Minor differences in inertia

Yellow Position; Black Force; Blue Information

Position
- Location or components
- Predecessor frame + motion / rotation
- Defines system inertia

Force
- Mechanical models
- Not a physical object that you can pick up and hold

Information
- Signals
- Just like Simulink

White Reference Frame; Yellow Transformed Frame; Grey Force Terminal; Unconnected White Ground Reference Frame

Rigid Bodies
- Reference frame aligns with Transformed frame of previous element
- Position & Rotation Angles Transform frame

White Reference Frame; Flexible Members & Animation Bodies; hidden; just for looks but looks good

Force Elements
- No fixed length
- 2 Reference Frames (White)
- Reaction force
- Closed kinematic chains

Animation Bodies
- No dynamic effect
- Visual representation only
- No explicit connection (yellow) to model
- Physical spring hidden

Function Properties; Body Properties

Useful When
- Parameter used in multiple places
- Design parameter

# Holes


Hole
• Remove inertia from system
• Shaft not same material as Cap

# Holes

Cap | Hole

Negative; Equal

Same radius as shaft

Hole
• Remove inertia from system
• Shaft not same material as Cap

# Gear Sets


Spur Gear
- Power Transmission (1D) / Transmission Elements
- Reverses direction
- Specify losses

DC Machine
- Electro-Mechanics / Electric Machines / DC Machine
- Ground 1 terminal to avoid singularity

Controlled Voltage Source
- Electrical and Electronics / Analog / Basic Elements / Linear VCVS
- Electrical and Electronics / Analog / Sources / Voltage Source
- Ground 1 terminal to avoid singularity

Gain
- Signal Blocks / Linear Signal Blocks / Proportional Gain (P Gain)
- VCVS scales input by Voltage Source value (12 V)
- Divide by 12V to compensate

Help; Web Page

Getting Help
- Double-click what you are interested in
- Press F1
- Web-Page appears
- Other topics on left
- Search bar above

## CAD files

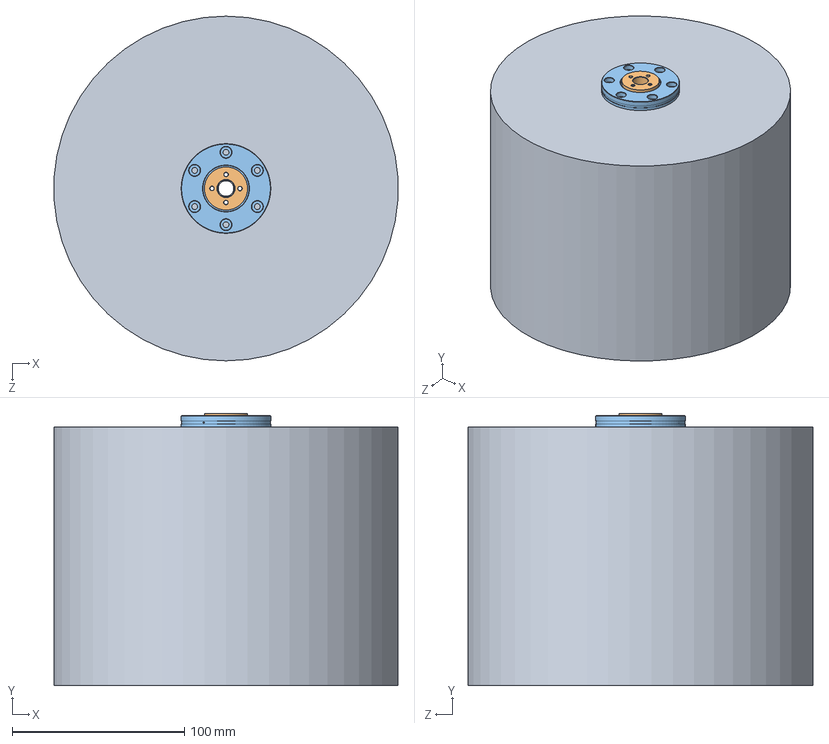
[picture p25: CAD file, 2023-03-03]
mechanical design/391 solidwork_1/simxbase.SLDASM
199.6 x 158.0 x 200.0 mm
pole
Inner2010N11_Face-Mount Crossed-Roller Bearing - 副本
2010N11_Face-Mount Crossed-Roller Bearing

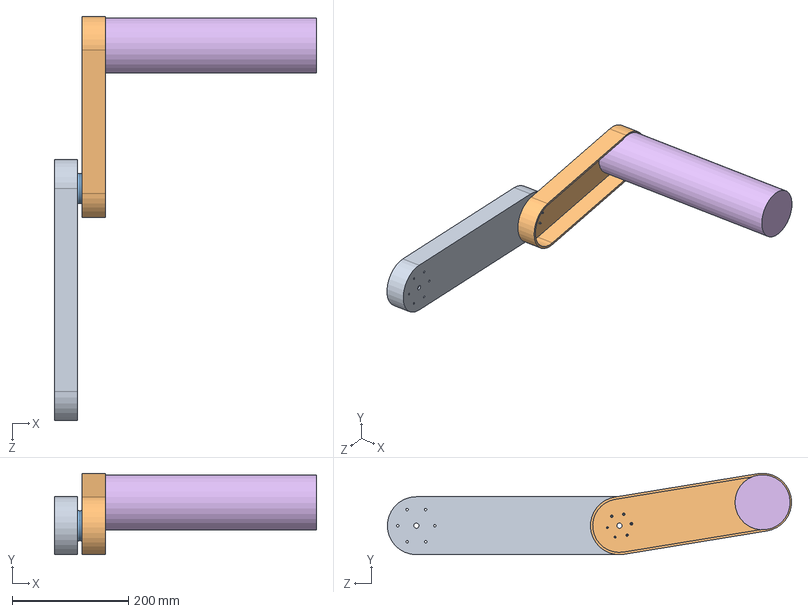
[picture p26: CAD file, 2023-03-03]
mechanical design/391 solidwork_1/twoArms_small.SLDASM
452.0 x 140.3 x 696.3 mm
机械臂
前机械臂
2010N11_Face-Mount Crossed-Roller Bearing
螺丝 x 10
Inner2010N11_Face-Mount Crossed-Roller Bearing - 副本
something

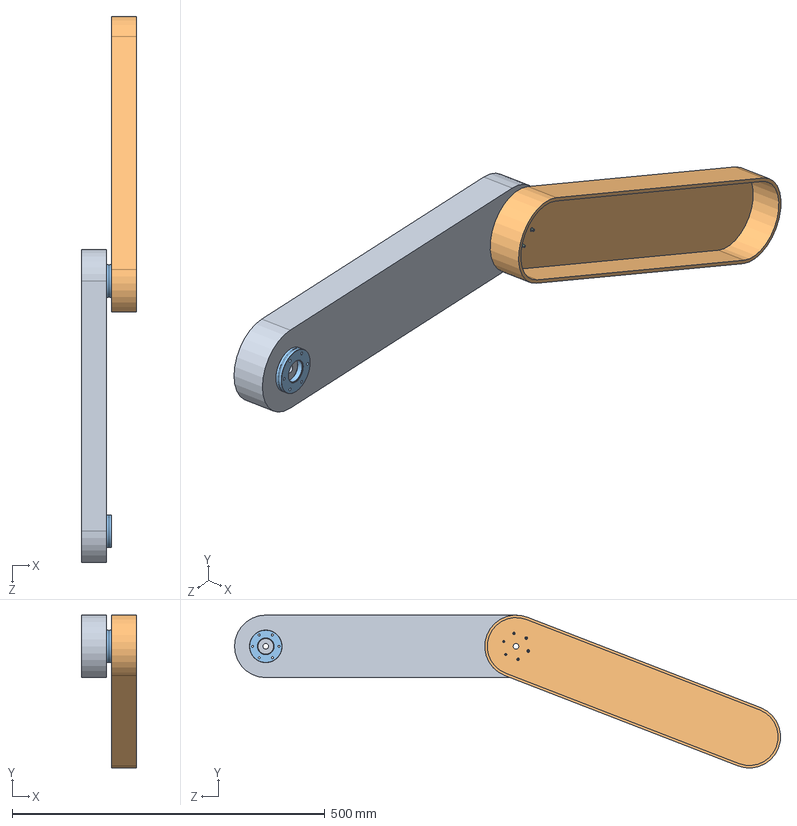
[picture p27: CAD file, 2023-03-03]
mechanical design/391 solidwork_1/twoarm.SLDASM
88.0 x 244.4 x 872.8 mm
机械臂
前机械臂
2010N11_Face-Mount Crossed-Roller Bearing x 2
螺丝 x 10
Inner2010N11_Face-Mount Crossed-Roller Bearing - 副本

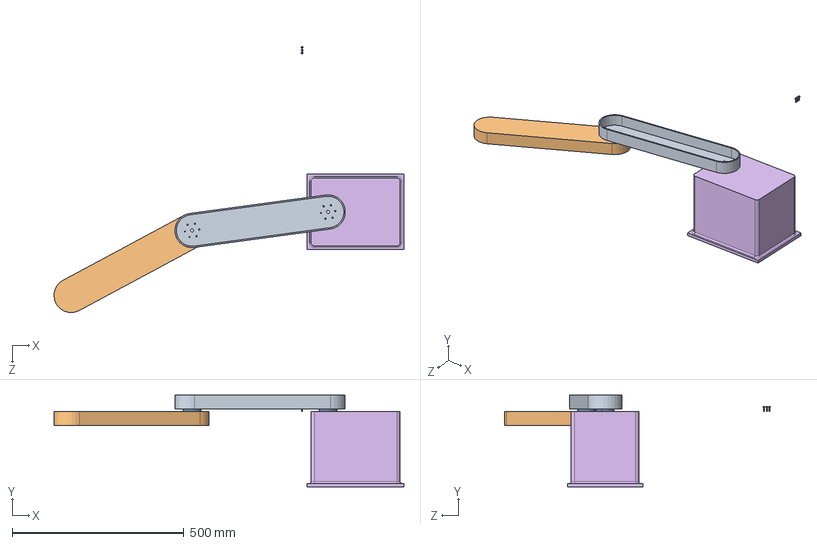
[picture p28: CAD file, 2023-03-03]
mechanical design/391 solidwork_1/twoArmsAndBase.SLDASM
1019.7 x 267.0 x 775.3 mm
机械臂
前机械臂
2010N11_Face-Mount Crossed-Roller Bearing x 2
螺丝 x 10
Inner2010N11_Face-Mount Crossed-Roller Bearing - 副本
base

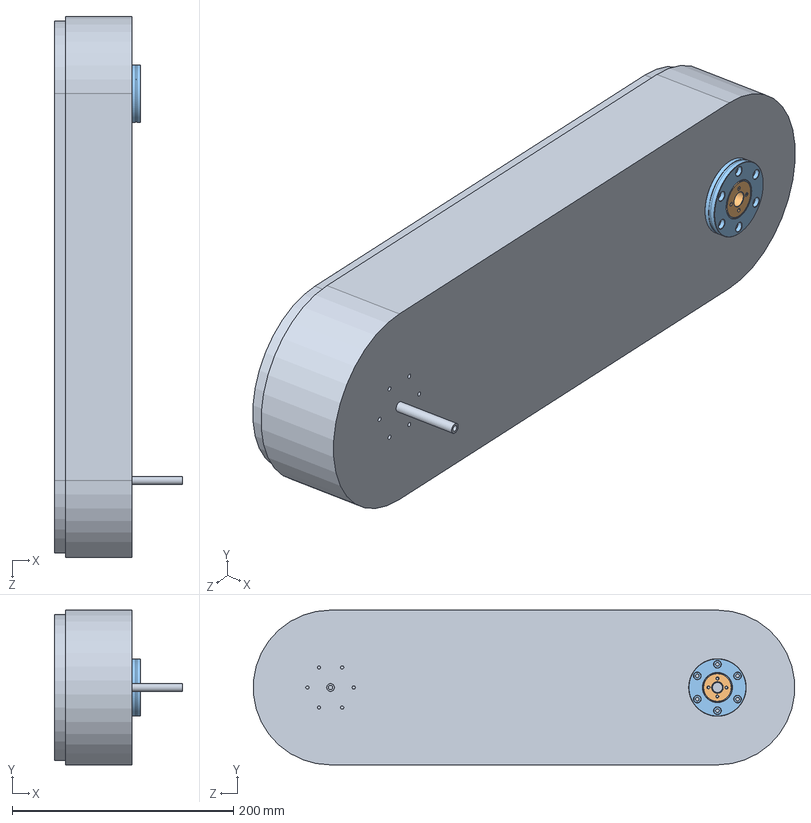
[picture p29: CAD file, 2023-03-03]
mechanical design/391 solidwork_1/simubigarm.SLDASM
116.0 x 140.0 x 489.4 mm
机械臂
Inner2010N11_Face-Mount Crossed-Roller Bearing - 副本
2010N11_Face-Mount Crossed-Roller Bearing
0.stp
0-0.stp
0-1.stp
0-2.stp
0-3.stp
57545K639_Steel Worm

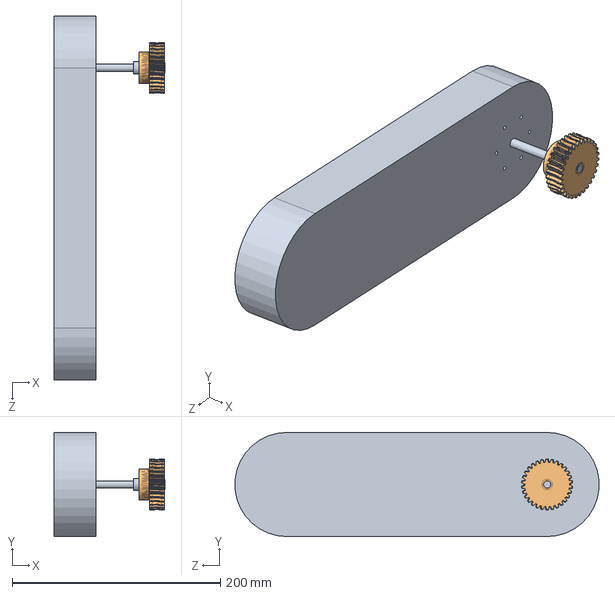
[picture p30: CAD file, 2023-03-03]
mechanical design/391 solidwork_1/simsmallarm.SLDASM
106.2 x 100.0 x 349.6 mm
前机械臂
57545K779_Metal Worm Gear

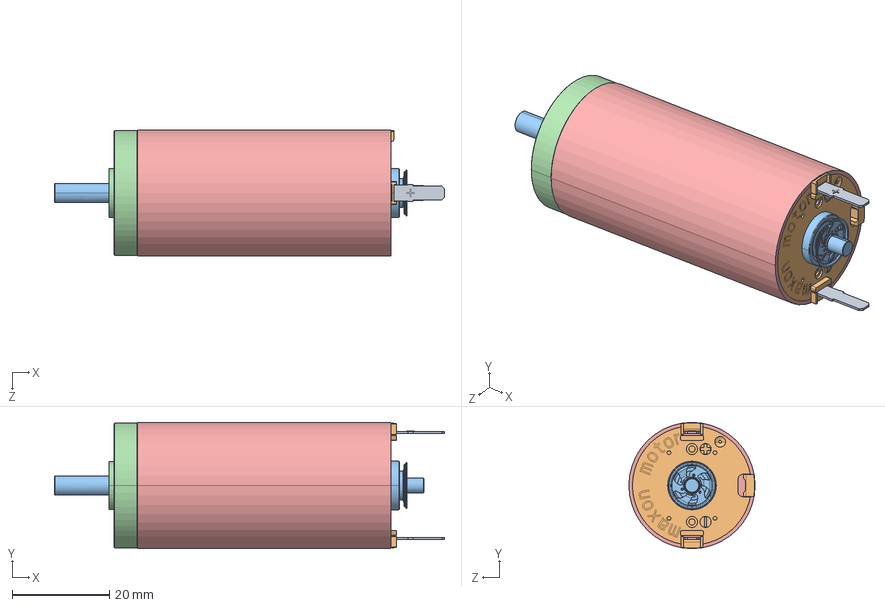
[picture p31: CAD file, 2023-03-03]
mechanical design/391 solidwork_1/0_1.SLDASM
80.3 x 26.0 x 26.0 mm
0.stp
0-0.stp
0-1.stp
0-2.stp
0-3.stp

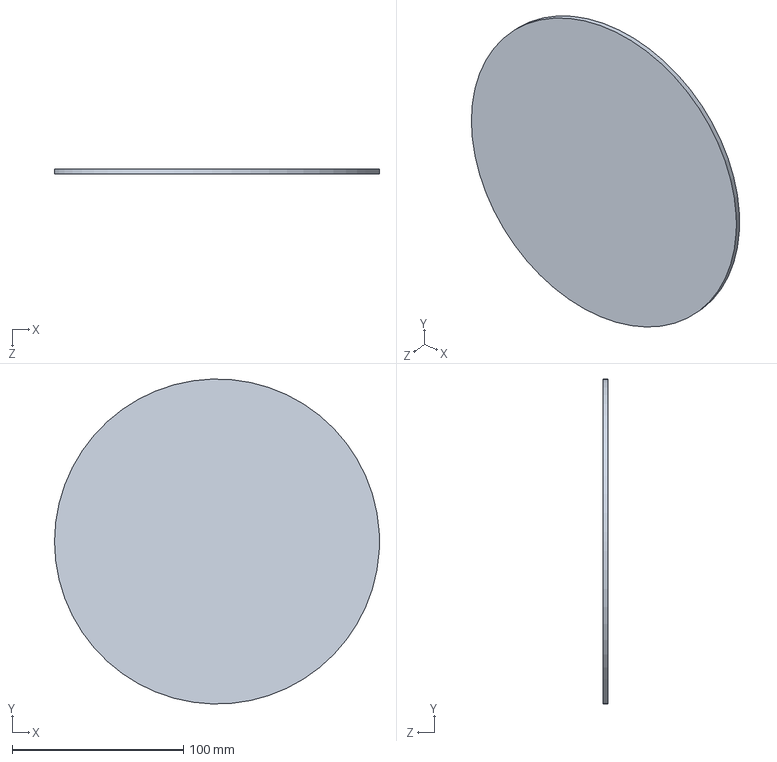
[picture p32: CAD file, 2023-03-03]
mechanical design/391 solidwork_1/盖子.SLDPRT
190.0 x 189.9 x 3.00 mm

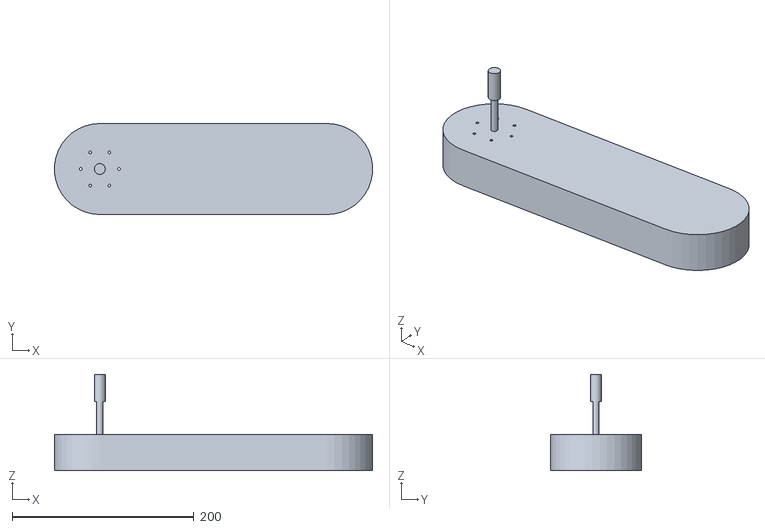
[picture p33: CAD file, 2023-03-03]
SimulationX/forearm.STL
349.7 x 100.0 x 106.0

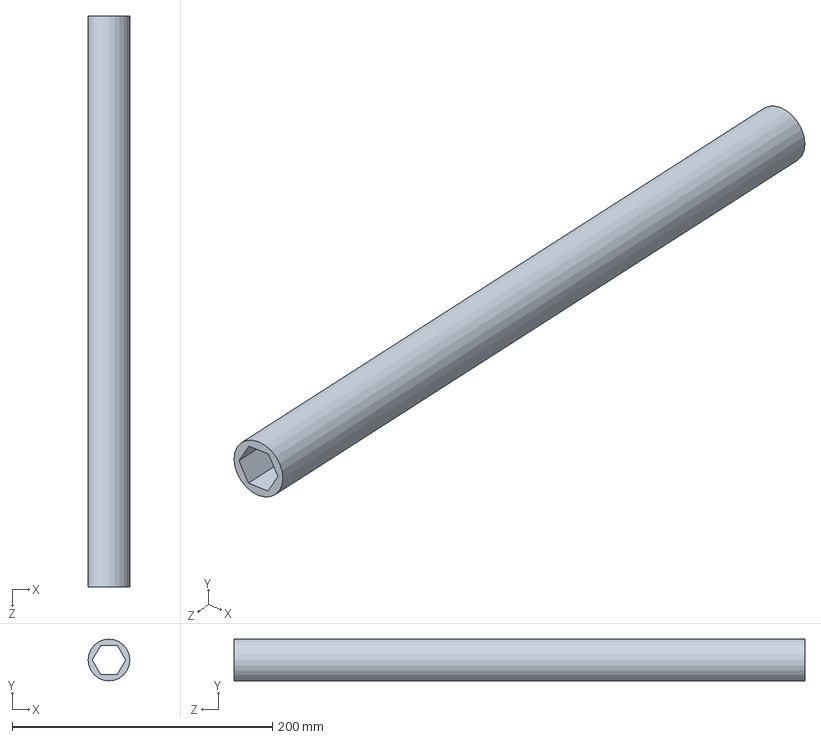
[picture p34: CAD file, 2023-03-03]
mechanical design/391 solidwork_1/竖直外壳.SLDPRT
32.1 x 32.1 x 439.0 mm

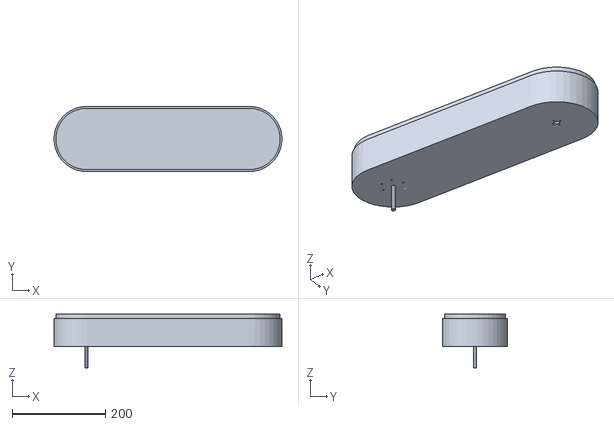
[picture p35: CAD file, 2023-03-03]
SimulationX/arm.STL
489.9 x 140.0 x 116.0

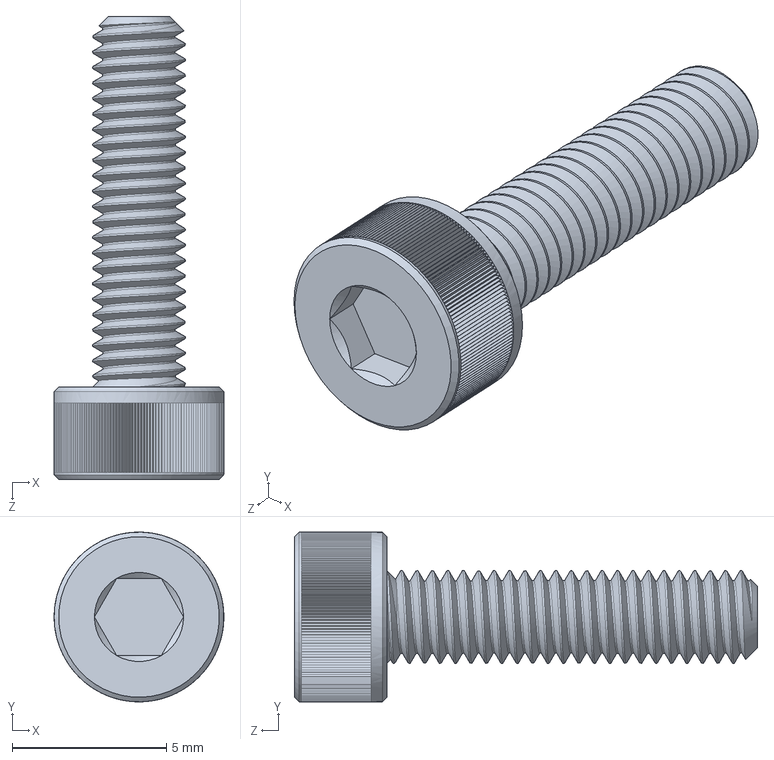
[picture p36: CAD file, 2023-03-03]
mechanical design/391 solidwork_1/螺丝.SLDPRT
5.50 x 5.50 x 15.0 mm

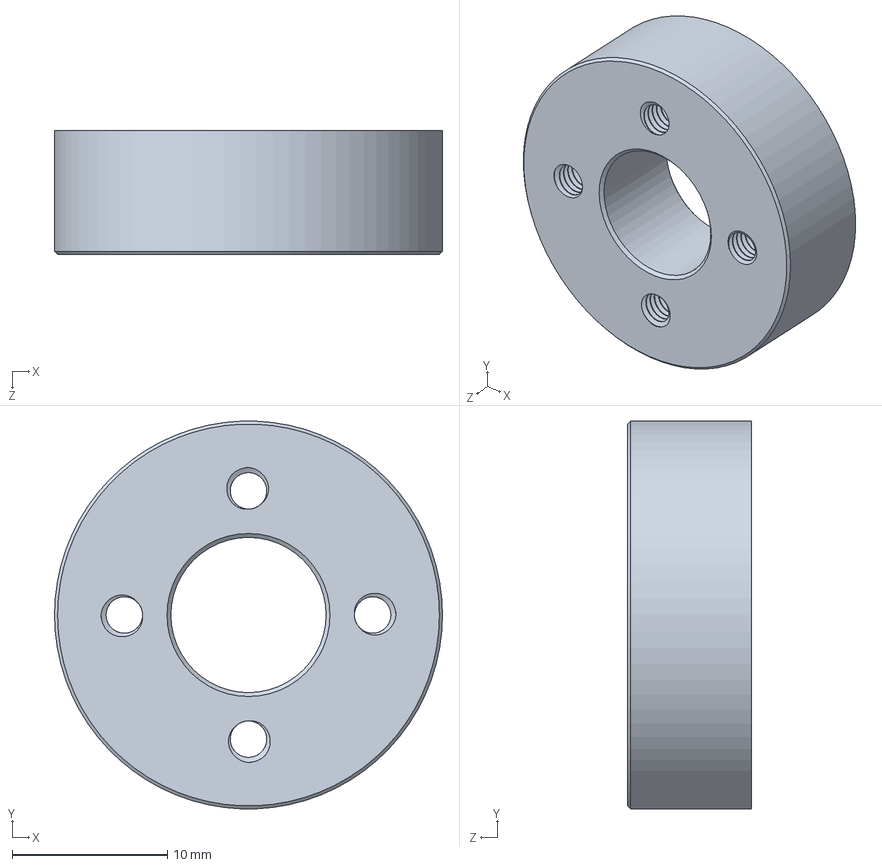
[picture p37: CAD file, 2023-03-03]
mechanical design/391 solidwork_1/Inner2010N11_Face-Mount Crossed-Roller Bearing - 副本.SLDPRT
25.0 x 25.0 x 8.00 mm

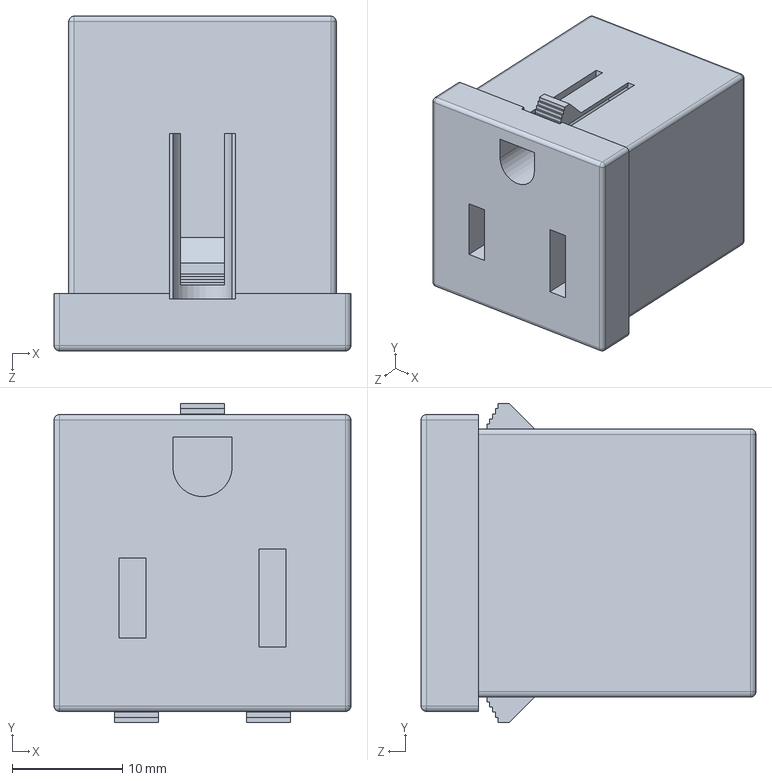
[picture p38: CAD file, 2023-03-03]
mechanical design/391 solidwork_1/7168K1_Panel-Mount Straight-Blade Receptacle.SLDPRT
26.9 x 28.9 x 30.4 mm

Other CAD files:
mechanical design/391 solidwork_1/Leadlong.SLDPRT
mechanical design/391 solidwork_1/arm2.STL
mechanical design/391 solidwork_1/fixer.SLDPRT
mechanical design/391 solidwork_1/前机械臂.SLDPRT
mechanical design/391 solidwork_1/0_1 (3).stp
mechanical design/391 solidwork_1/2010N11_Face-Mount Crossed-Roller Bearing.SLDPRT
mechanical design/391 solidwork_1/57545K639_Steel Worm.SLDPRT
mechanical design/391 solidwork_1/57545K644_Steel Worm.SLDPRT
mechanical design/391 solidwork_1/57545K779_Metal Worm Gear.SLDPRT
mechanical design/391 solidwork_1/57545K819_Metal Worm Gear.SLDPRT
mechanical design/391 solidwork_1/90592A085_Steel Hex Nut.SLDPRT
mechanical design/391 solidwork_1/91290A123_Black-Oxide Alloy Steel Socket Head Screw.SLDPRT
mechanical design/391 solidwork_1/LeadS.SLDPRT
mechanical design/391 solidwork_1/User Library-ArduinoMicro.sldprt
mechanical design/391 solidwork_1/arm1.STL
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
